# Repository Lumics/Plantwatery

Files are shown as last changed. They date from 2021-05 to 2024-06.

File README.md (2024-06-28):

# Plantwatery

A project of Anna Dai and Maurin Widmer.

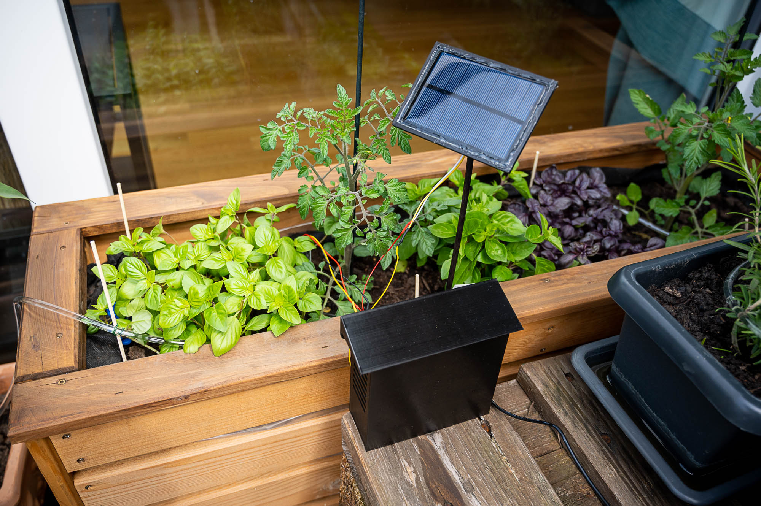
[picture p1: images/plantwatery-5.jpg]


## Summary

Plantwatery is an automated watering system for your garden plants. It is based on an ESP32, a capacitive soil moisture sensor, solar cell & battery and a water pump. The system is autonomous and measures twice per day the soil moisture and operates the pump if needed. It's collected data and status is send via Wifi (MQTT protocol) to the cloud. All parts can easily be bought and the case is 3D printed (drawings are provided). The plastic housing is constructed to protect it's inner electronic parts from water and makes it easy to attach the solar panel, water pump and soil sensor.

The code is written with the Arduino framework and can easily be adapted to other platforms. 
It allows to change watering time & hours of the day, soil sensor offset and MQTT topics. Furthermore, the code automatically checks if a new version is online and updates itself if there is (for example because you want to change some parameters like soil sensor offset or watering time). 

## Changelog

### Version 12
Updated Version June 2024
* Adding a TPS61023 from Adafruit for a stable boost from 3.7V to 5V. This helps to make the usage of the ESP32 much more reliable if the voltage dropped
* Bug fixes to improve deep sleep cycle
* Improved battery monitor output
* Improved Hum reading and new wiring to ESP32 directly for power to decrease power flowing through sensor over time

### Version 9
Updated Version from 31.12.2022 includes:
* a LDO and capacitors in the electronics. Furthermore the standard ESP32 is used to further save battery power (no LED). Sketch is updated accordingly.
* Updated code with more reliable computing of how many seconds are needed until ESP32 needs to wake up to water the plants.

### Version 8
Inital Version

## Hardware

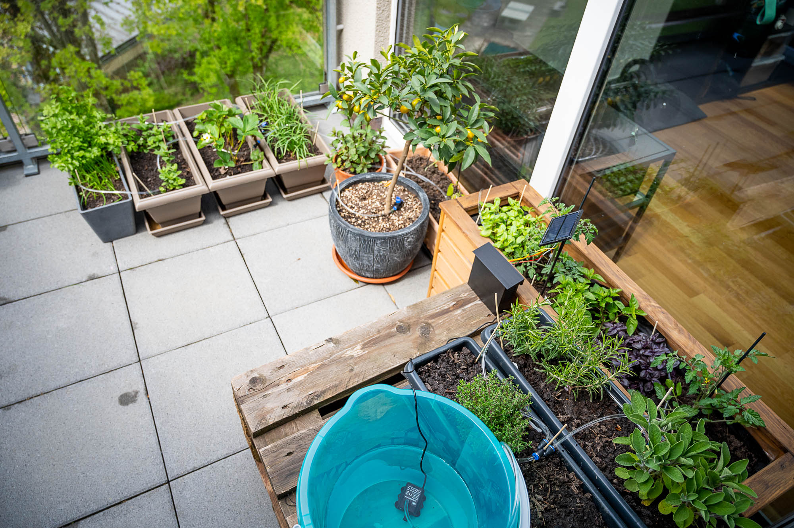
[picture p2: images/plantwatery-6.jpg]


In the following you have a list of suggestions of parts you need to build this project. 

### Control unit:
* Microcontroller [ESP32 devkit](https://www.aliexpress.com/item/33048962331.html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,searchweb201602_,searchweb201603_)
* Relay or Mosfet to control pump: [IRF520N Mosfet board](https://www.aliexpress.us/item/3256802178204101.html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)
* Battery Management Board: [TP4056](https://www.aliexpress.com/item/4000522397541.html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,searchweb201602_,searchweb201603_)
* Battery holder: [18650 Case](https://www.aliexpress.com/item/1005001707889794.html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,searchweb201602_,searchweb201603_)
* Battery: [18650 Lithium Rechargeable Battery 3.7V](https://www.aliexpress.com/item/32324914059.html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,searchweb201602_,searchweb201603_)
* PCB Prototype board to solder the wires together and add the connectors: [PCB Prototype Board](https://www.aliexpress.com/item/32588853051.html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,searchweb201602_,searchweb201603_)
* Low voltage regulator: [LDO MCP1700-3302E](https://www.aliexpress.us/item/3256801422024433.html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)
* Resistor: [27kOhm](https://www.aliexpress.us/item/2251832772049066.html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) and [100kOhm](https://www.aliexpress.us/item/2251832772049066.html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)
* Capacitor: [100uF](https://www.aliexpress.us/item/3256801889213205.html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) and [100nF](https://www.aliexpress.us/item/3256802138966377.html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)
* Cable connector: [PCB Screw Terminal](https://www.aliexpress.com/item/1000006518504.html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,searchweb201602_,searchweb201603_)
* Jumper cables: [Dupont Jumper Wire](https://www.aliexpress.com/item/32911287776.html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,scm-url:1007.13339.169870.0,pvid:9e77f922-b1ed-43af-a189-ed38dffac609,tpp_buckets:668%230%23131923%2362_668%230%23131923%2362_668%23888%233325%235_668%23888%233325%235_668%232846%238110%231995_668%235811%2327182%2353_668%232717%237560%23222_668%231000022185%231000066059%230_668%233468%2315608%23187_668%232846%238110%231995_668%235811%2327182%2353_668%232717%237560%23222_668%233164%239976%23952_668%233468%2315608%23187)
and some [longer cables](https://www.aliexpress.com/item/4000009001537.html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,searchweb201602_,searchweb201603_)
* 3D printed housing

### Solar part:
* [Solar cell 5V, 200mA](https://www.aliexpress.com/item/32906698984.html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,searchweb201602_,searchweb201603_)
* 3D printed housing
* Some hot glue to make it waterproof
* Wooden stick to mount the housing

### Soil measuring part:

* Soil sensor: [Capacitive Soil Sensor](https://www.aliexpress.com/item/32832538686.html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,searchweb201602_,searchweb201603_)
* Some hot glue to make the electronics part waterproof

### Water part:

* Water pump, around 5V but they also work with 3.7V: [Mini Brushless Water Pump 5V, 2.4W](https://www.aliexpress.com/item/32995965702.html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,searchweb201602_,searchweb201603_)
* Tubes, I got the 6mm (outside) as they fit perfectly inside of the pump fixture: [Tubes](https://www.aliexpress.com/item/4000859747207.html?spm=a2g0s.9042311.0.0.7d434c4d9Ae92m) 
* Connectors for the tubes (6mm): [Pipe connector](https://www.aliexpress.com/item/4001338085412.html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,scm-url:1007.13339.169870.0,pvid:5e90a557-ecfb-47ad-835c-de327359bc74,tpp_buckets:668%230%23131923%2357_668%230%23131923%2357_668%23888%233325%235_668%23888%233325%235_668%232846%238110%231995_668%235811%2327180%2341_668%232717%237562%23492_668%231000022185%231000066059%230_668%233468%2315607%2396_668%232846%238110%231995_668%235811%2327180%2341_668%232717%237562%23492_668%233164%239976%23386_668%233468%2315607%2396)
* Stopper for the end of the tubes: [Stopper connector](https://www.aliexpress.com/item/4000027416210.html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,scm-url:1007.13339.169870.0,pvid:22fbe9bb-979b-482c-955a-72fbf8ae5a17,tpp_buckets:668%230%23131923%2357_668%230%23131923%2357_668%23888%233325%235_668%23888%233325%235_668%232846%238110%231995_668%235811%2327180%2341_668%232717%237562%23492_668%231000022185%231000066059%230_668%233468%2315607%2396_668%232846%238110%231995_668%235811%2327180%2341_668%232717%237562%23492_668%233164%239976%23386_668%233468%2315607%2396)
* Large bucket
* Maybe some wooden sticks and some wire to hold the tubes in place

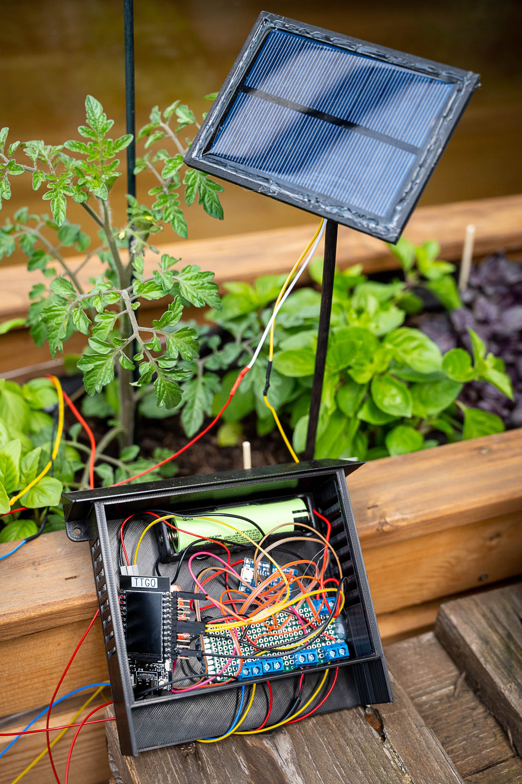
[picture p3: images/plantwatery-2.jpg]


(Picture above showing Plantwatery version 8)

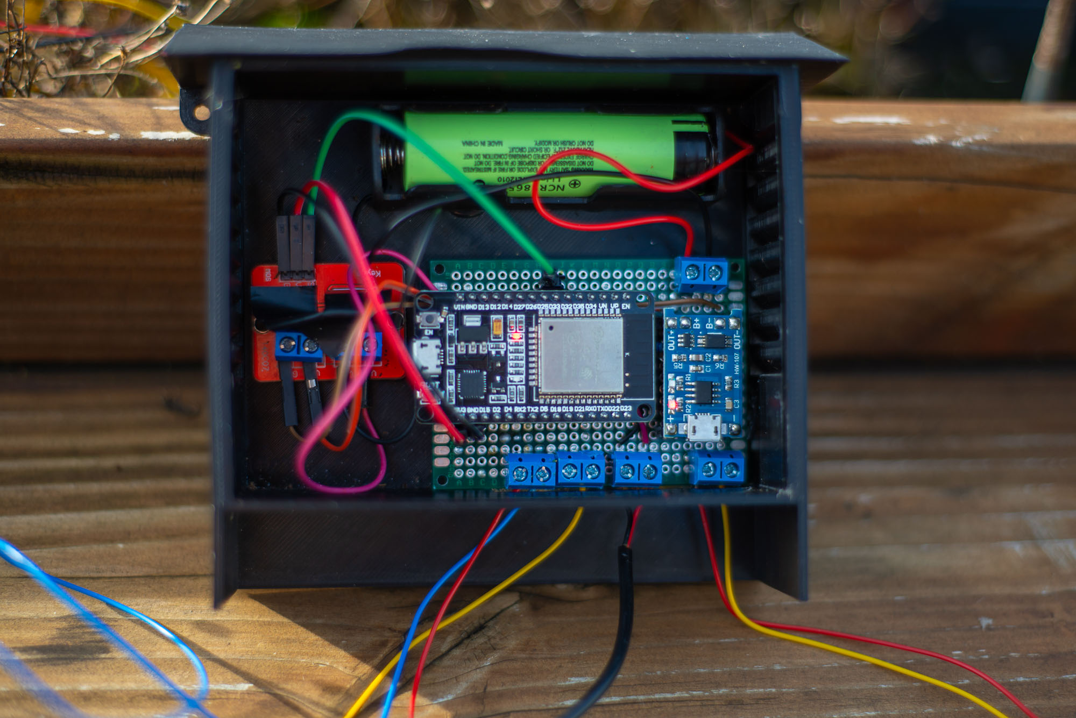
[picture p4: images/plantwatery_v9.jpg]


(Picture above showing Plantwatery version 9, see changelog)

## Electronics / Sketch

Here you can find a sketch of the wiring for the electronic components. It should be straight forward. I recommend to use some screw terminals to attach the longer wires of the external humidity sensor, pump and solar cell (compare image). Moreover, make sure to add the low voltage regulator as shown in the sketch. This makes sure that the esp32 works at 3.3V. Additionaly, the added capacitors help to smoothen out the supply voltage from potential voltage spikes. 

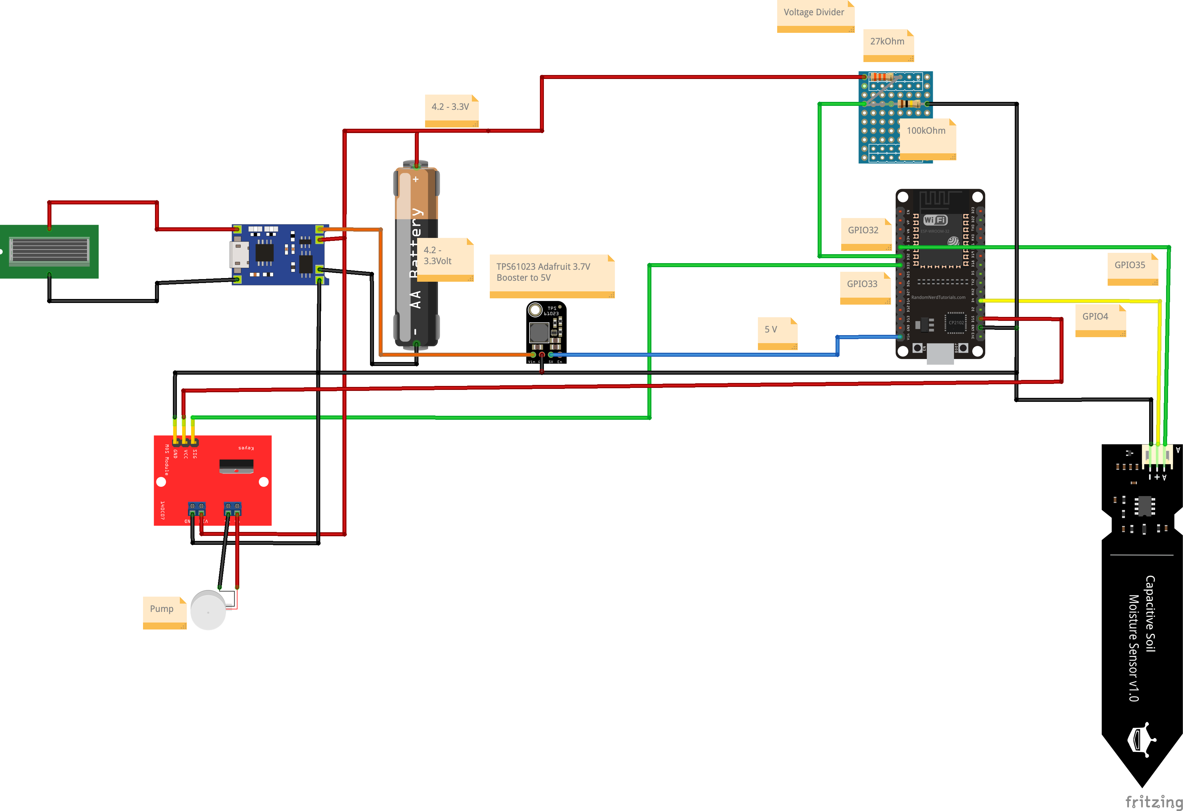
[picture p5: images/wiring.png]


The drawings for the casing for all parts can be found in the folder: housing.

## Watering system

The tubes were connected to the pump and then placed between the plants. We used a Y connector to go to all plants and always have a small tube which has some self made small holes at the spots where it should water the plants. Therefore, we only have to change the tubes with the holes, if we rearrange the plants or want suddenly smaller holes.

## Code
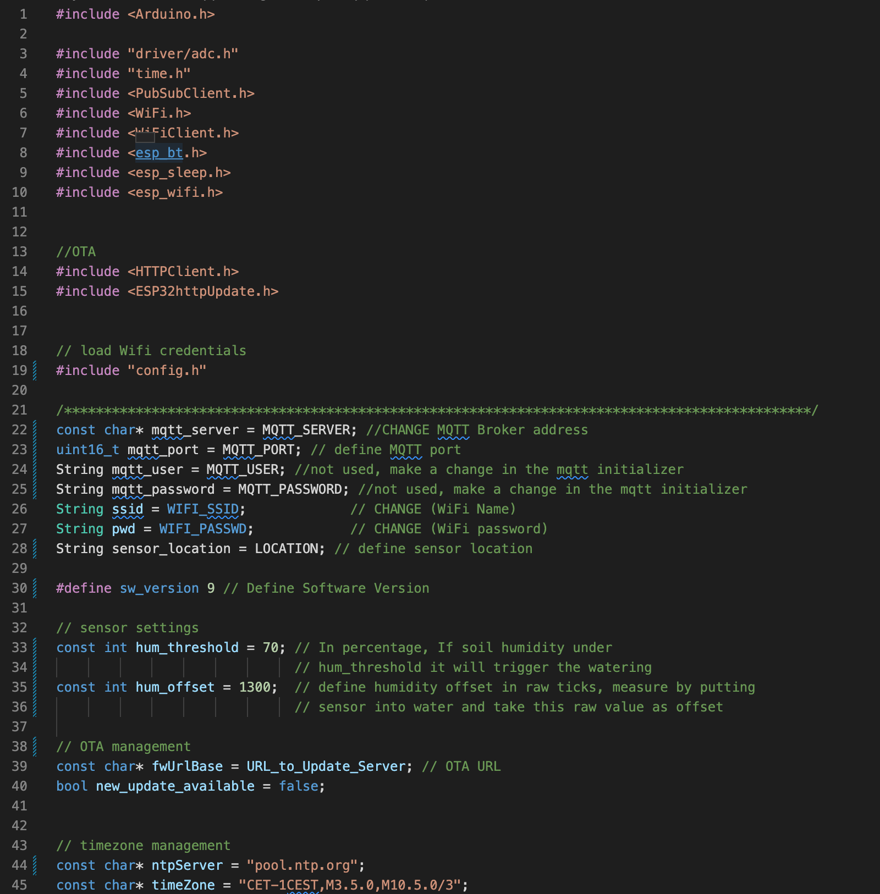
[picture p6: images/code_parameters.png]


To code is written for the Arduino framework with the PlatformIo IDE. Please make sure to add a file called: "config.h" to the src folder (copy and rename the config_example.h and fill in the details). If you do not have a OTA server you can just leave the URL like it is or remove everything with OTA from the code. 

Make sure to change the hum_threshold, hum_offset and the watering times according to your needs.

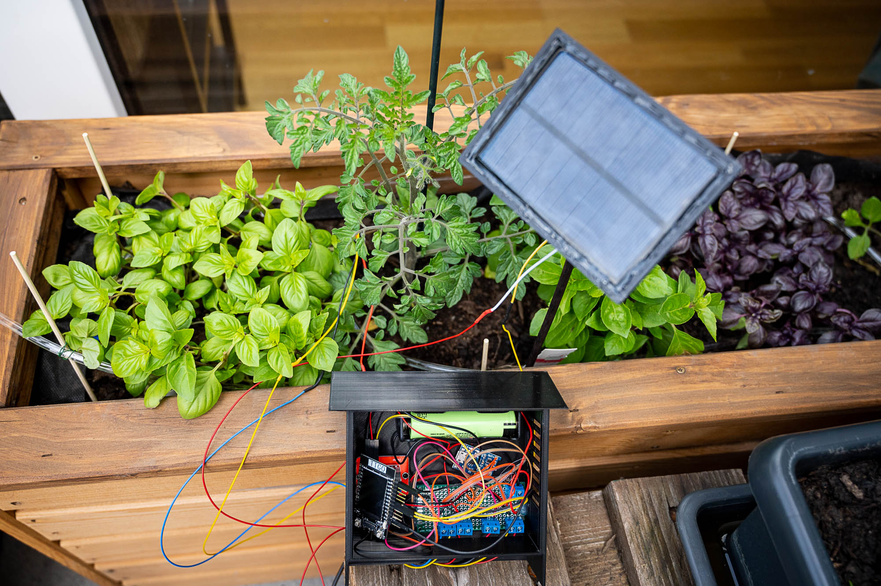
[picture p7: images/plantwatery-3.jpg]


Have fun with the project and let us know if you have a question or if you build this. 

## ToDo 

### Further power improvement suggestion to investigate incase the kit uses too much power to recharge via solar cell
* Either switch the ESP32 devkit board with a board without the CP2102, regulator and power LED
* Scrap the power LED to get approx another 2mA power saving 
* Increase amount of solar cell and put them in series
* Add an Resistor to the TP4056 as shown in the video of [Andreas Spiess](https://www.youtube.com/watch?v=37kGva3NW8w)
* Try to use a different board lige TTGO T18 with many components integrated

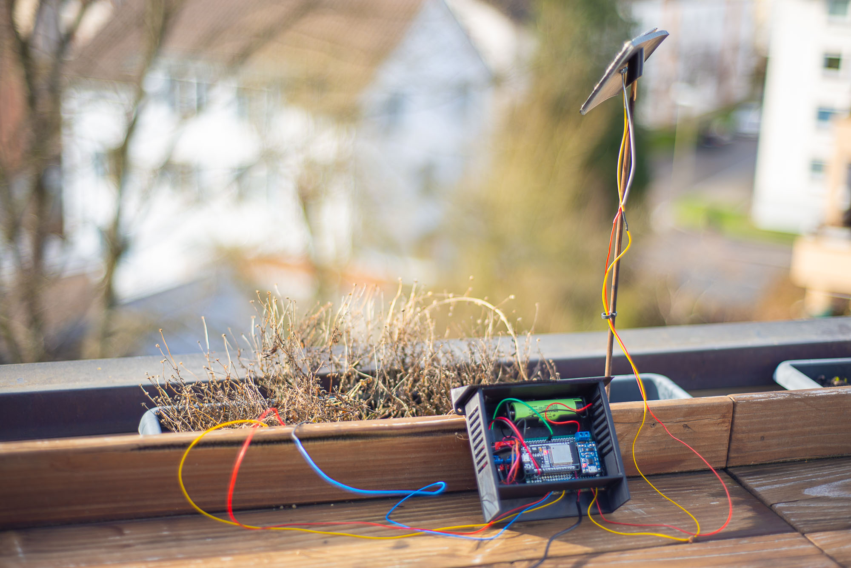
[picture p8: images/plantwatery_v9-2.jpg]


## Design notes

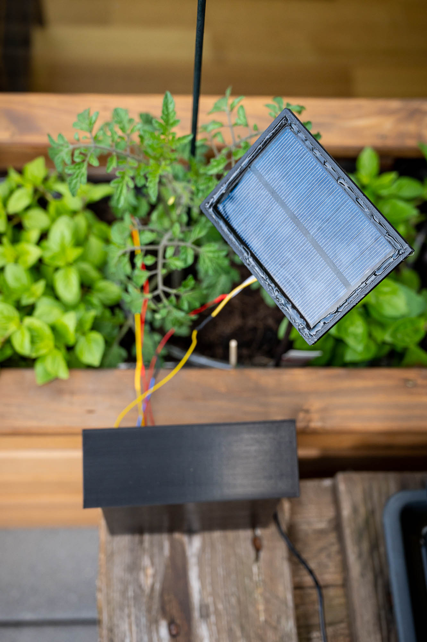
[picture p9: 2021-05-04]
images/plantwatery-4.jpg

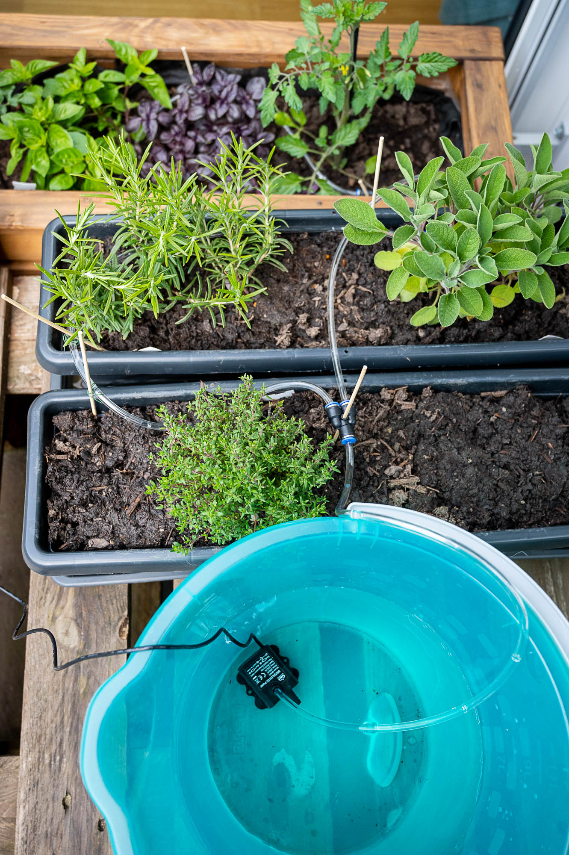
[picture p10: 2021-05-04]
images/plantwatery.jpg

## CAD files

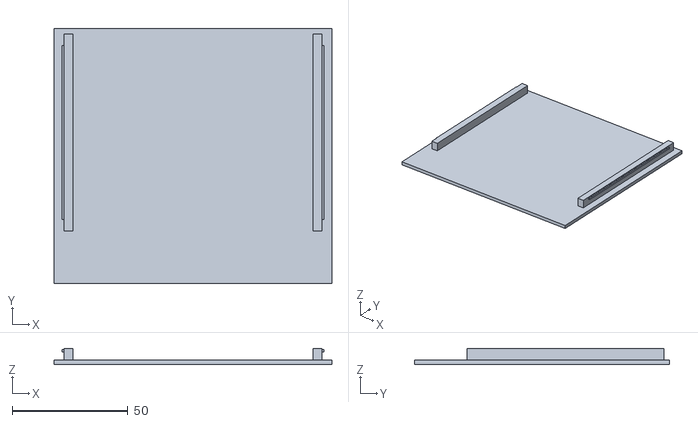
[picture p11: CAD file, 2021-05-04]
housing/deckel.STL
120.0 x 110.0 x 7.00

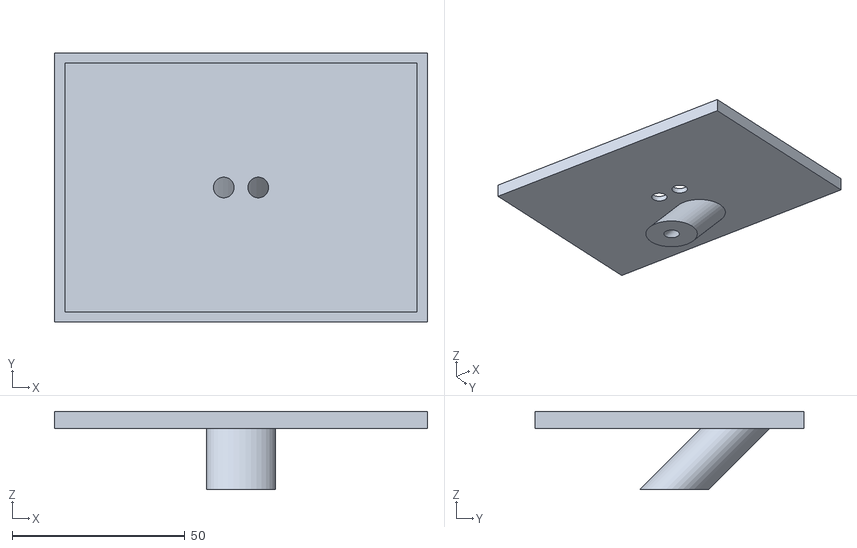
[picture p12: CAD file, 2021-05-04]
housing/SolarPanel.STL
108.0 x 78.0 x 22.7

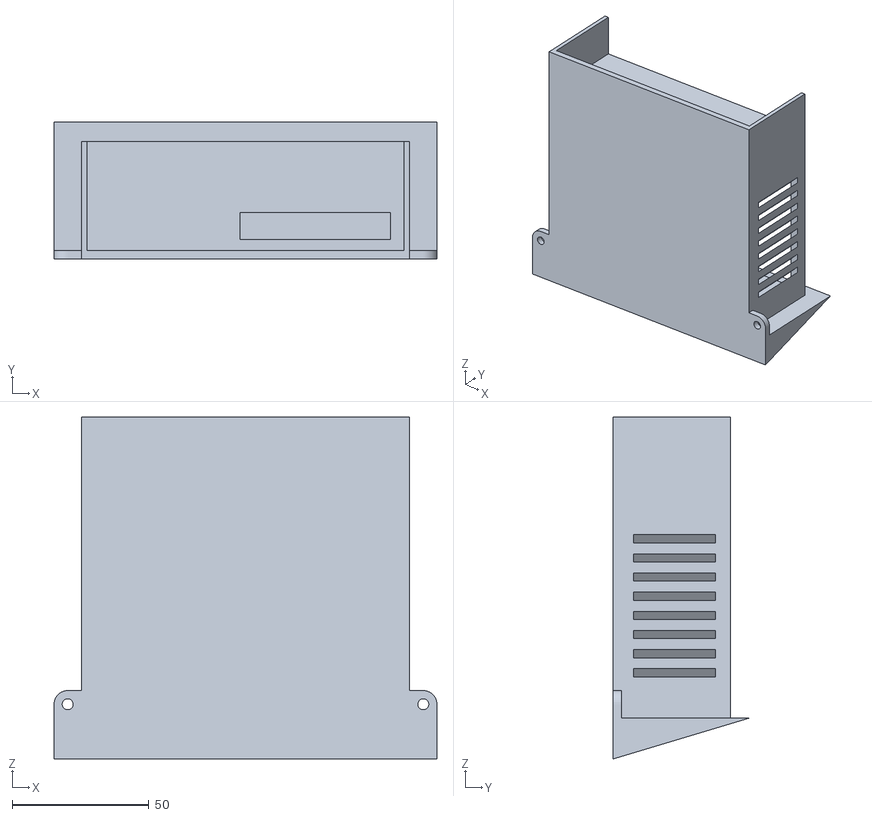
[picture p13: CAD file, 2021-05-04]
housing/bottom.STL
140.0 x 50.0 x 125.0

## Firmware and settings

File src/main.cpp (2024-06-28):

#include <Arduino.h>

#include "driver/adc.h"
#include "time.h"
#include <PubSubClient.h>
#include <WiFi.h>
#include <WiFiClient.h>
#include <esp_bt.h>
#include <esp_sleep.h>
#include <esp_wifi.h>


//OTA
#include <HTTPClient.h>
#include <ESP32httpUpdate.h>


// load Wifi credentials
#include "config.h"

/**********************************************************************************************/
const char* mqtt_server = MQTT_SERVER; //CHANGE MQTT Broker address
uint16_t mqtt_port = MQTT_PORT; // define MQTT port
String mqtt_user = MQTT_USER; //not used, make a change in the mqtt initializer
String mqtt_password = MQTT_PASSWORD; //not used, make a change in the mqtt initializer
String ssid = WIFI_SSID;             // CHANGE (WiFi Name)
String pwd = WIFI_PASSWD;            // CHANGE (WiFi password)
String sensor_location = LOCATION; // define sensor location

#define sw_version 12 // Define Software Version

// sensor settings
const int hum_threshold = 80; // In percentage, If soil humidity under
                              // hum_threshold it will trigger the watering
const int hum_offset = 1071;  // define humidity offset in raw ticks, measure by putting
                              // sensor into water and take this raw value as offset

// OTA management
const char* fwUrlBase = URL_to_Update_Server; // OTA URL
bool new_update_available = false;


// timezone management
const char* ntpServer = "pool.ntp.org";
const char* timeZone = "CET-1CEST,M3.5.0,M10.5.0/3";

// watering time
const int watering_hour_am = 7;       // 7 am
const int watering_hour_pm = 19;      // 7 pm
const int watering_time = 100 * 1000;  // in milli seconds

// *** Hardware Definitions ***
#define Pin_pump 33         // define esp pin for triggering pump
#define Pin_humi_sensor 35  // define analog pin to read from humidity sensor
#define Pin_voltage_divider 32  // define analog pin to read from voltage divider for battery voltage
#define Pin_vcc_humidity_sensor 4 // define esp pin to give vcc to the humidity sensor (only when ESP32 is awake)
// when wifi active only ADC1 available GPIO32 - GPIO39


uint64_t uS_TO_S_FACTOR = 1000000; //Conversion factor for micro seconds to seconds 
#define wifi_timeout 5000L  // 5 seconds in milliseconds

// *** persistent data ***
RTC_DATA_ATTR int bootCount = 0;  // Boot count should be stored in the non volatile RTC Memory
RTC_DATA_ATTR struct tm last_watering_time;  // Parameters see:
                         // http://www.cplusplus.com/reference/ctime/tm/
RTC_DATA_ATTR time_t now;

/***********************************************************************************************/

int hum_raw = 0;

String mac;
String MAC_ADDRESS;
WiFiClient espClient;
PubSubClient client(espClient);
String sensor_topic = "sensors/soil";
String device_type = "ESP32";
String device_name = "esp32_plantwatery";
int wifi_setup_timer = 0;


void setup_wifi() {
    char ssid1[30];
    char pass1[30];
    ssid.toCharArray(ssid1, 30);
    pwd.toCharArray(pass1, 30);
    Serial.println();
    log_i("Connecting to: %s", ssid1);
    WiFi.mode(WIFI_STA);
    WiFi.begin(ssid1, pass1);
    while (WiFi.status() != WL_CONNECTED) {
        delay(10);
        Serial.print(".");
        wifi_setup_timer++;
        if (wifi_setup_timer >
            999) {  // Restart the ESP if no connection can be established
            ESP.restart();
        }
    }
    Serial.println("");
    log_i("WiFi connected");
    log_i("IP address: %s", WiFi.localIP().toString());
}

void check_for_OTA(){
  new_update_available = false;  
  String fwURL = String( fwUrlBase );
  String fwVersionURL = fwURL;
  fwVersionURL.concat( "firmware.version" );

  log_i( "Checking for firmware updates." );
  log_i( "Firmware version URL: %s ", fwVersionURL);

  HTTPClient httpClient;
  httpClient.begin( fwVersionURL );
  int httpCode = httpClient.GET();
  if( httpCode == 200 ) {
    String newFWVersion = httpClient.getString();

    log_i( "Current firmware version: %d", sw_version );
    log_i( "Available firmware version: %s", newFWVersion );

    int newVersion = newFWVersion.toInt();

    if( newVersion > sw_version ) {
        new_update_available = true;
      log_i( "Preparing to update" );

      String fwImageURL = fwURL;
      fwImageURL.concat( "firmware.bin" );
      t_httpUpdate_return ret = ESPhttpUpdate.update( fwImageURL );

      switch(ret) {
        case HTTP_UPDATE_FAILED:
          log_i("HTTP_UPDATE_FAILD Error (%d): %s", ESPhttpUpdate.getLastError(), ESPhttpUpdate.getLastErrorString().c_str());
          break;

        case HTTP_UPDATE_NO_UPDATES:
          log_i("HTTP_UPDATE_NO_UPDATES");
          break;

        case HTTP_UPDATE_OK:
          log_i("HTTP_UPDATE_OK");
          break;
      }
    }
    else {
      log_i( "Already on latest version" );
    }
  }
  else {
    log_i( "Firmware version check failed, got HTTP response code %d", httpCode );
  }
  httpClient.end();
}

void goToDeepSleep(uint64_t sleepTime_sec) {
    // testing
    // sleepTime_sec = 30;
    log_i("Going to sleep for %f seconds", (double)sleepTime_sec);
    client.disconnect();
    delay(300);
    WiFi.disconnect(true);
    WiFi.mode(WIFI_OFF);
    btStop();
    delay(300);
    esp_wifi_stop();
    esp_bt_controller_disable();

    // Configure the timer to wake us up!
    uint64_t sleeptime = sleepTime_sec * uS_TO_S_FACTOR; // needed to sleep long enough
    esp_err_t error = esp_sleep_enable_timer_wakeup(sleeptime);
    Serial.println(error);
    delay(1000);  // give enough time to print everything to serial
    Serial.flush();  
    // Go to sleep! Zzzz
    esp_deep_sleep_start();
    log_e("this should not happen");
}

void print_wakeup_reason() {
    esp_sleep_wakeup_cause_t wakeup_reason;

    wakeup_reason = esp_sleep_get_wakeup_cause();

    switch (wakeup_reason) {
        case 1:
            log_i("Not a wakeup cause, used to disable all wakeup sources");
            break;
        case 2:
            log_i("Wakeup caused by external signal using RTC_IO");
            break;
        case 3:
            log_i("Wakeup caused by external signal using RTC_CNTL");
            break;
        case 4:
            log_i("Wakeup caused by timer");
            break;
        case 5:
            log_i("Wakeup caused by touchpad");
            break;
        case 6:
            log_i("Wakeup caused by ULP program");
            break;
        case 7:
            log_i("Wakeup caused by GPIO");
            break;
        case 8:
            log_i("Wakeup caused by UART");
            break;
        default:
            log_i("Wakeup was not caused by deep sleep");
            break;
    }
}

void setTimeZone() {
    struct tm timeinfo;
    configTime(0, 0, ntpServer);
    if(!getLocalTime(&timeinfo)){
        log_e("Failed to obtain time");
    } else {
        log_i("Got the time from the NTP Server");
    }
    delay(100);
    setenv("TZ", timeZone, 1);
    delay(200);
    tzset();
}

bool isTimeToWater() {
    time(&now);
    struct tm curr_time;
    localtime_r(&now, &curr_time);
    char strftime_buf[64];
    strftime(strftime_buf, sizeof(strftime_buf), "%c", &curr_time);
// If the day is the same and the hour diff is smaller or equal to 1 then it should not water
    if (curr_time.tm_mday == last_watering_time.tm_mday && 
                (abs(curr_time.tm_hour - last_watering_time.tm_hour) <= 1)){
      strftime(strftime_buf, sizeof(strftime_buf), "%c", &last_watering_time);
      log_i("Just watered at %s, go back to sleep", strftime_buf);
        return false;
    } else if (curr_time.tm_hour == watering_hour_am ||
        curr_time.tm_hour == watering_hour_pm) {
        log_i("It's time to water the plants");
        return true;
    } 
    log_i("Don't water yet it's only %s", strftime_buf);
    return false;
}

uint64_t setSleepTime() {
    uint64_t sleepTimeS = 43000;  // define standard as about 12h 
    time(&now);
    struct tm curr_time;
    localtime_r(&now, &curr_time);
    char strftime_buf[64];
    strftime(strftime_buf, sizeof(strftime_buf), "%c", &curr_time);
    log_i("current time: %s", strftime_buf);
    uint64_t seconds = 0;
    if (curr_time.tm_hour >= watering_hour_am &&
        curr_time.tm_hour < watering_hour_pm) {
        // compute watering time in the evening
        struct tm evening;
        localtime_r(&now, &evening);
        evening.tm_hour = watering_hour_pm;
        evening.tm_min = 0;
        evening.tm_sec = 0;
        seconds = difftime(mktime(&evening), now);
        log_i("%f seconds until next watering from now", (double)seconds);
        strftime(strftime_buf, sizeof(strftime_buf), "%c", &evening);
        log_i("Time to water in the evening: %s", strftime_buf);
    } else if (curr_time.tm_hour >= 0 &&
        curr_time.tm_hour < watering_hour_am) {
        // compute watering time between midnight and morning of the same day
        struct tm early_morning;
        localtime_r(&now, &early_morning);
        early_morning.tm_hour = watering_hour_am;
        early_morning.tm_min = 0;
        early_morning.tm_sec = 0;
        seconds = difftime(mktime(&early_morning), now);
        log_i("%f seconds until next watering from now", (double)seconds);
        strftime(strftime_buf, sizeof(strftime_buf), "%c", &early_morning);
        log_i("Time to water in the morning: %s", strftime_buf);
    } else {
        struct tm morning;
        localtime_r(&now, &morning);
        morning.tm_hour = watering_hour_am;
        morning.tm_min = 0;
        morning.tm_sec = 0;
        morning.tm_mday = curr_time.tm_mday + 1;  // next day
        seconds = difftime(mktime(&morning), now);
        log_i("%f seconds until next watering from now", (double)seconds);
        strftime(strftime_buf, sizeof(strftime_buf), "%c", &morning);
        log_i("Time to water in the morning the next day: %s", strftime_buf);
    }
 
    sleepTimeS = (uint64_t)seconds;
    //sleepTimeS = (uint64_t) 300; // to debug, wake up every 5min
    log_i("Set sleep time to %f [s]", (double)sleepTimeS);
    return sleepTimeS;
}

void printLocalTime() {
    time(&now);
    struct tm curr_time;
    localtime_r(&now, &curr_time);
    char strftime_buf[64];
    strftime(strftime_buf, sizeof(strftime_buf), "%c", &curr_time);
    log_i("The current date/time in Zurich is: %s", strftime_buf);
}

void printLastWateringTime() {
    char strftime_buf[64];
    strftime(strftime_buf, sizeof(strftime_buf), "%c", &last_watering_time);
    log_i("Last watering time is: %s",
          asctime_r(&last_watering_time, strftime_buf));
}

void setLastWateringTime() {
    time(&now);
    localtime_r(&now, &last_watering_time);
    char strftime_buf[64];
    strftime(strftime_buf, sizeof(strftime_buf), "%c", &last_watering_time);
    log_i("Set last watering time to: %s", strftime_buf);
}

// Reconnect to the MQTT server
void reconnect() {
    // keep track of when we started our attempt to get a wifi connection
    unsigned long startAttemptTime = millis();
    while (!client.connected() && millis() - startAttemptTime < wifi_timeout) {
        log_i("Attempting MQTT connection...");
        char id[mac.length() + 1];
        mac.toCharArray(id, mac.length() + 1);
        if (client.connect(id)) {
            log_i("connected");
        } else {
            log_i("failed, rc= %s try again in 5 seconds", client.state());
            delay(100);
        }
    }
}

float measure_battery_level() {
    float batteryLevel = map(analogRead(Pin_voltage_divider), 2696.0f, 4095.0f, 0, 100); // 2696 = 2.7V, 4095 = 4.1V
    log_i("Battery level measured is: %f", batteryLevel);
    return batteryLevel;
}

void setup() {
    delay(200); //Helps with common issue that ESP32 is not waking up after deep sleep 
    Serial.begin(115200);
    pinMode(Pin_pump, OUTPUT);
    pinMode(Pin_vcc_humidity_sensor, OUTPUT);

    log_i("Setup");
    // Wifi
    setup_wifi();                         // connect to wifi
    client.setServer(mqtt_server, 1883);  // connect wo MQTT server
    MAC_ADDRESS = WiFi.macAddress();      // get MAC address
    Serial.println(MAC_ADDRESS);
    mac = MAC_ADDRESS.substring(9, 11) + MAC_ADDRESS.substring(12, 14) +
          MAC_ADDRESS.substring(
              15,
              17);  // shorten MAC address to the last four digits (without ":")

    if (WiFi.status() != WL_CONNECTED) {
        reconnect();
    }
    // initialize time zone and get the time
    setTimeZone();
    printLocalTime();
    log_i("Setup done.");

    digitalWrite(Pin_vcc_humidity_sensor, HIGH); // give voltage to the humidity sensor


    // One time Execution before deep sleep, therefore not in the loop
    if (!client.connected() && WiFi.status() == WL_CONNECTED) {
        reconnect();
    }
    client.loop();
    log_i("Sensor location: %s", sensor_location);
    bootCount++;
    log_i("Boot count: %d", bootCount);
    print_wakeup_reason();
    printLastWateringTime();

    hum_raw = analogRead(Pin_humi_sensor);
    digitalWrite(Pin_vcc_humidity_sensor, LOW); // Turn off power again to the humidity sensor
    log_i("Raw Soil Sensor value: %d", hum_raw);
    float soil_hum = map(hum_raw, hum_offset, 4095.0f, 100, 0);
    log_i("Moisture: %.1f %%", soil_hum);
    client.publish(
        (sensor_topic + "/Humidity").c_str(),
        ("SOIL_RH,site=" + sensor_location + " value=" + String(soil_hum))
            .c_str(),
        false);
    client.publish(
        (sensor_topic + "/BatteryVoltage").c_str(),
        ("BatteryVoltage,site=" + sensor_location + " value=" + String(measure_battery_level())).c_str(),
        false);
    client.publish(
            (sensor_topic + "/SoftwareVS").c_str(),
            ("SoftwareVS,site=" + sensor_location + " value=" + String(sw_version)).c_str(),
            false);
    log_i("MQTT Published Soil RH, Battery Voltage and Software Version: %d", sw_version);
    delay(100);

    if (isTimeToWater()) {
        if (soil_hum < hum_threshold) {
            digitalWrite(Pin_pump, HIGH);
            log_i("the soil is too dry. water plants now for %d s",
                  watering_time / 1000);
            delay(watering_time);
            digitalWrite(Pin_pump, LOW);
            setLastWateringTime();
            if (!client.connected() && WiFi.status() == WL_CONNECTED) {
                reconnect();
            }
            
            client.publish(
                (sensor_topic + "/Watered").c_str(),
                ("WATERED,site=" + sensor_location + " value=" + String(1))
                    .c_str(),
                false);
            log_i("Publish watered data");
            delay(500);

        } else {
            client.publish(
                (sensor_topic + "/Watered").c_str(),
                ("WATERED,site=" + sensor_location + " value=" + String(0))
                    .c_str(),
                false);
            log_i("MQTT Publish too humid, did not water plant");
            delay(300);
        }
    } else {
        client.publish(
            (sensor_topic + "/Watered").c_str(),
            ("WATERED,site=" + sensor_location + " value=" + String(0)).c_str(),
            false);
        log_i("MQTT Publish Woke up too early");
        delay(300);
    }
    
    if (!client.connected() && WiFi.status() == WL_CONNECTED) {
        reconnect();
    }
    client.loop();
    check_for_OTA();
    goToDeepSleep(setSleepTime());
}

void loop() {
// not used due to deep sleep
}

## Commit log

2022-12-31 Version 9
    [Plantwatery_wiring.fzz]
2023-01-09 Bug fix wrong decision to water
    [main.cpp]
2024-06-28 changed timeing behaviour to improve deep sleep
    [Plantwatery_wiring.fzz]
